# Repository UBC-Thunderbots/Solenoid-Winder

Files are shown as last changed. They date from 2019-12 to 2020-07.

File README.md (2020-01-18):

# Solenoid Winder

This is a project to produce a solenoid winding machine to wind the solenoids
for UBC ThunderBots. It uses a design inspired by a 3D printer z-axis to
guide the wire onto a rotating solenoid body.

We use a control board designed for a laser cutter or other small CNC machine
to drive the steppers. The particular one used is the
["Akozon 3D Printer Engraving Expansion Board Kit Controller CNC Shield V4"](https://www.amazon.ca/gp/product/B07DS2T64W/)
with the Arduino Nano clone that comes with it. It should be noted that this
board contains a bug: the microstepping jumpers are configured to pull down
the configuration pins on the drivers (which have internal pull-downs),
meaning that there is no way to set the MS1, MS2 or MS3 pins to high. Due to
this bug, the drivers are forced to full steps. We may hack the stepper
driver boards so they have a bodge wire to directly pull these pins up and
cut the pins going to the buggy mainboard.

The winder is controlled by serial commands. I suggest
[CompuPhase Termite](https://www.compuphase.com/software_termite.htm) on
Windows to control the winder.

### Setup

The solenoid winder board must be connected to a 12v source. We usually use
one of the ThunderBots lab power supplies, set to a current of 1.5A. This
*only* powers the stepper motors, meaning that you can use the serial command
line interface without the external power on.

Due to the habit of the rotational stepper motor to heat up uncomfortably
quickly when it is left on, it is advised to turn off the power supply while
not actively winding. It is a possible future project to replace this stepper
with one that doesn't do that.

Attach the core to the rotational hub with M3 socket head cap screws (keep
these in the hub while not in use!). Feed the wire through the arm on the
carriage, then through one of the four holes in the solenoid core to retain
the end. These are slightly tricky to get the wire through: curve it slightly
to help it along.

Set up the spool holder at least 30cm away from the winder while in use in
order to avoid any possible inconsistencies caused by winding of the source
spool. I usually use a big bar clamp to stick it to the table.

If the winder is doing something bad, you can stop it by pressing the reset
button on the blue microcontroller board, or by turning off the motor power
supply. Either of these actions will safely bring the winder to a halt.

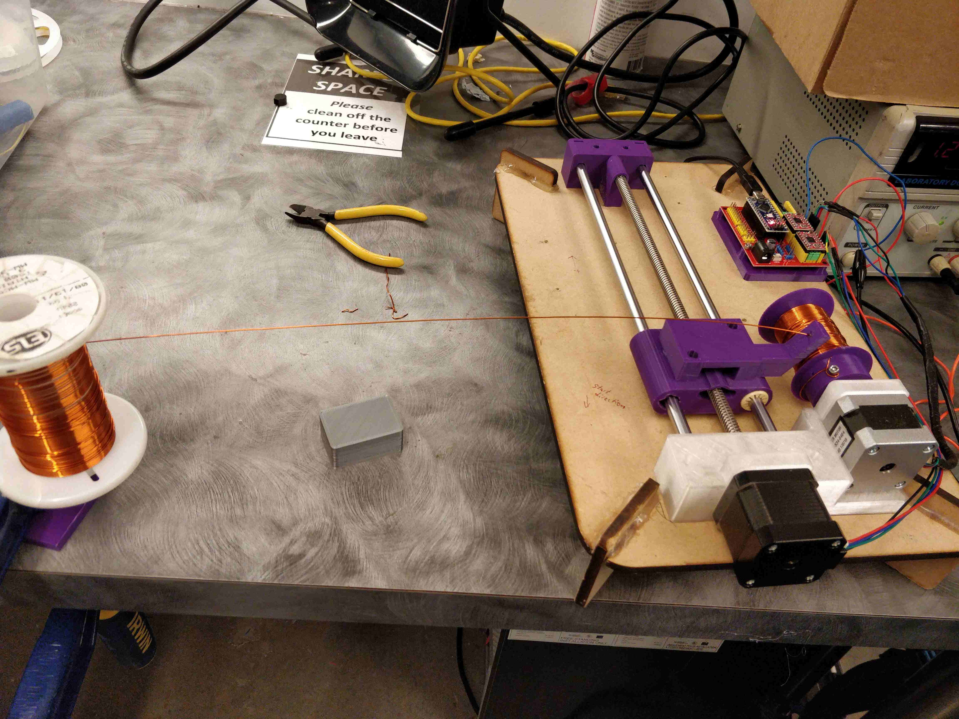
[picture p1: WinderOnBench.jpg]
photo of winder on the bench


### Operation

Set up your spool width with `spool_width {width in mm}`. Note that you
should set this about 5mm shorter than the actual spool width to avoid
overshooting the end of the spool.

Set the wire width: `wire_width {width in mm}`. This should have a
fudge-factor on it (oversize by ~5%) to ensure that the wire does not
inadvertently wind backwards: the current design of having an arm fairly
close to the spool means that if the winder does start winding in a backwards
direction, it can get back on track, but it is likely a better idea to simply
wind with a tiny bit of extra room.

Then, you can move the carriage either by slowly rotating the lead screw by
hand with the power off or by using `move_lateral {distance_in_mm}`. Note
that the positive direction is marked on the base of the winder and is
oriented away from the stepper on the lead screw.

Once you have the spool width and the wire width set up, you can start
winding by running `go {n_passes}`.

The winder will wind initially in the positive direction as marked on the
board (away from the rotational motor).

Note that each winding back and forth is
counted as two passes. See the diagram below:

```
║     ║        ║     ║
║     ║        ║_____║
╠═════╣ ---->  ╠═════╣
║    ↑║ 1 pass ║‾‾‾‾‾║
║    |║        ║↑    ║
    arm        arm
```

Also, the direction is reversed after every pass but is retained between runs
of the `go` command. This means that if you have already wound some turns and
want to wind some more, you can safely type `go 1` for example, and put on
another layer. If you want to start from the beginning, type `reset`.

Some tension is required on the wire in order to get it to go on straight.
This can be achieved by putting one's finger on the spool or with something
more advanced. Also, the winder itself is not really possible to clamp to the
table and wants to slide around.

## Development

This project is developed using [PlatformIO](https://platformio.org/).

To build from the command line: `platformio run`

To upload from the command line (note that you need to disconnect your
Termite window before uploading or it will fail to upload):
`platformio run -t upload`.

## Board documentation

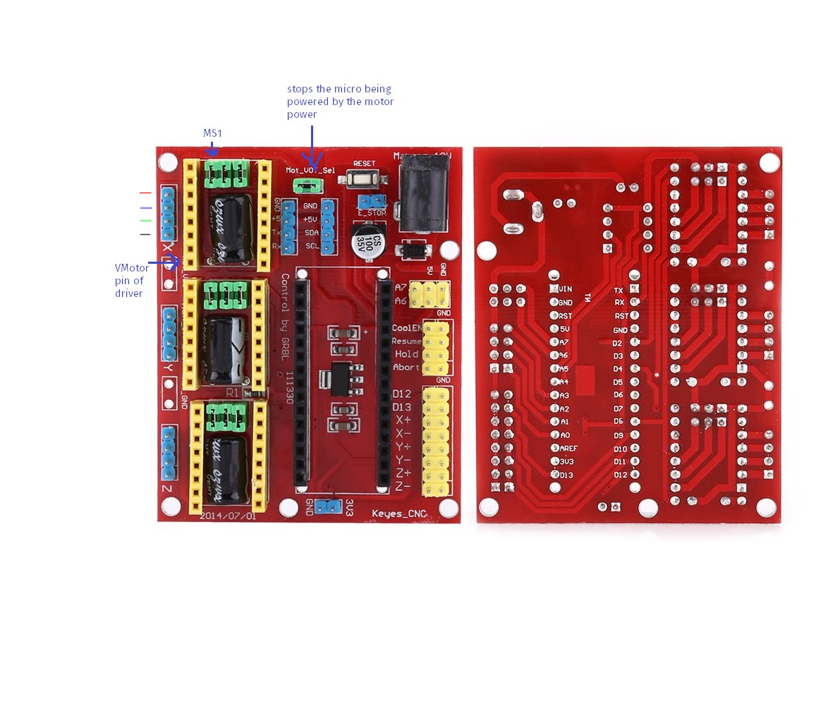
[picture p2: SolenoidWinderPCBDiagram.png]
board docs photo


## Future improvements

- Replace the rotational stepper motor with one that doesn't heat up quite as
  much
- Change the feet to something more flat and sturdy so it is possible to
  clamp the winder to the table
- Put proper connectors on the power input and stepper motors
- Tailstock?
- Hack the stepper driver boards by installing bodge wires and cutting the
  CFG pins on the headers so we get microstepping (currently it does full
  stepping because of a bug in the control board where the configuration pins
  should have a pull-up on the other side of the jumpers but actually have a
  pull-down)

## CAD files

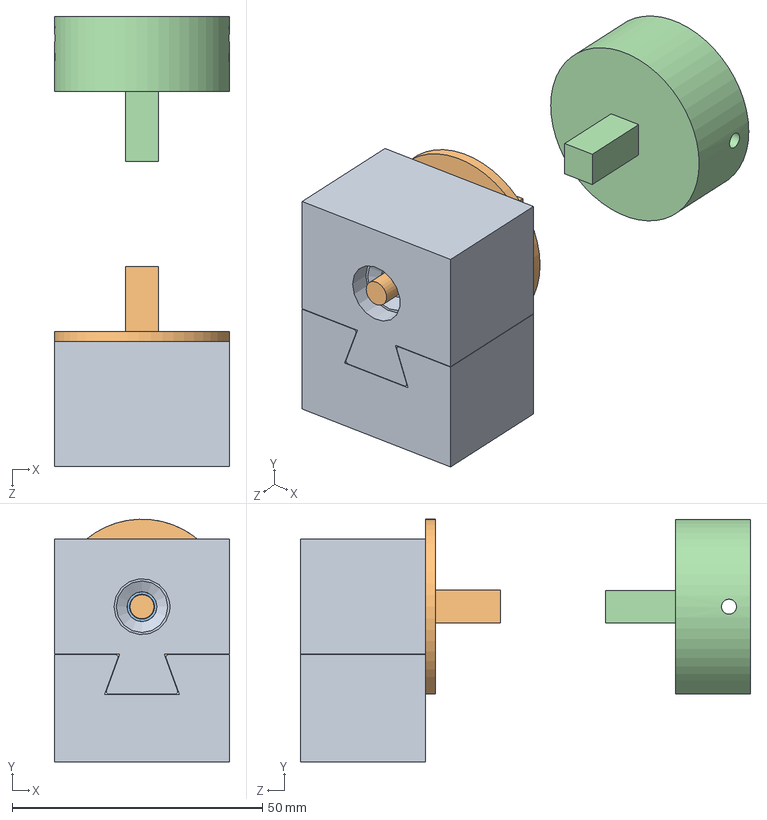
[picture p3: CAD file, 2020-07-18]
CAD/ThunderBots 2020 Headstock and Tailstock.SLDASM
35.0 x 48.5 x 90.0 mm
Tailstock Mount
Tailstock
bearing
SquareHub

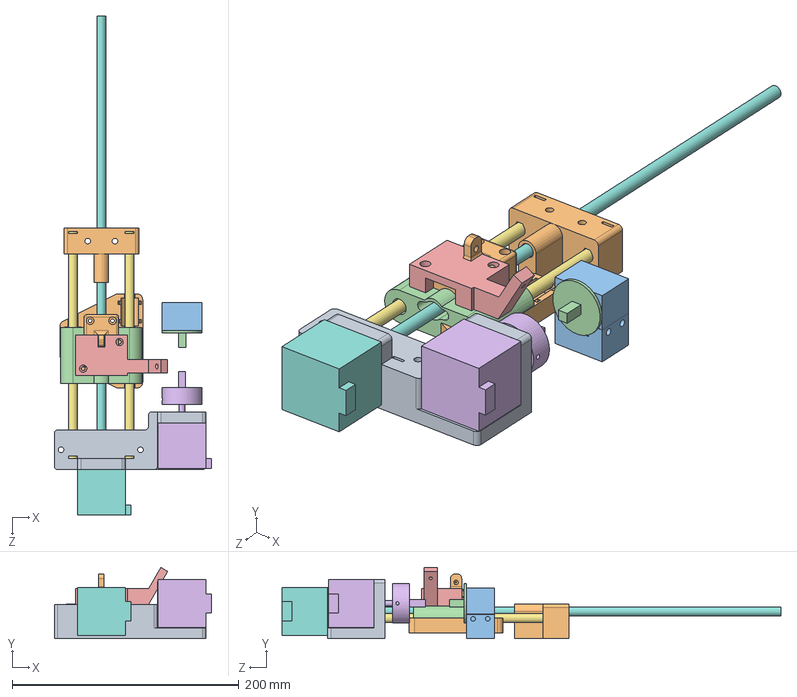
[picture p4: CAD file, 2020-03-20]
CAD/FullWinder.SLDASM
138.8 x 62.8 x 440.0 mm
SpinnyLeadScrewNut
New Main Part^Carriage
V2 Guide^Carriage
NormalStepper
Rod^FullWinder x 2
MotorEndBracket^FullWinder
Free End Cap^FullWinder
Tailstock Mount
Tailstock
bearing x 2
SquareHub

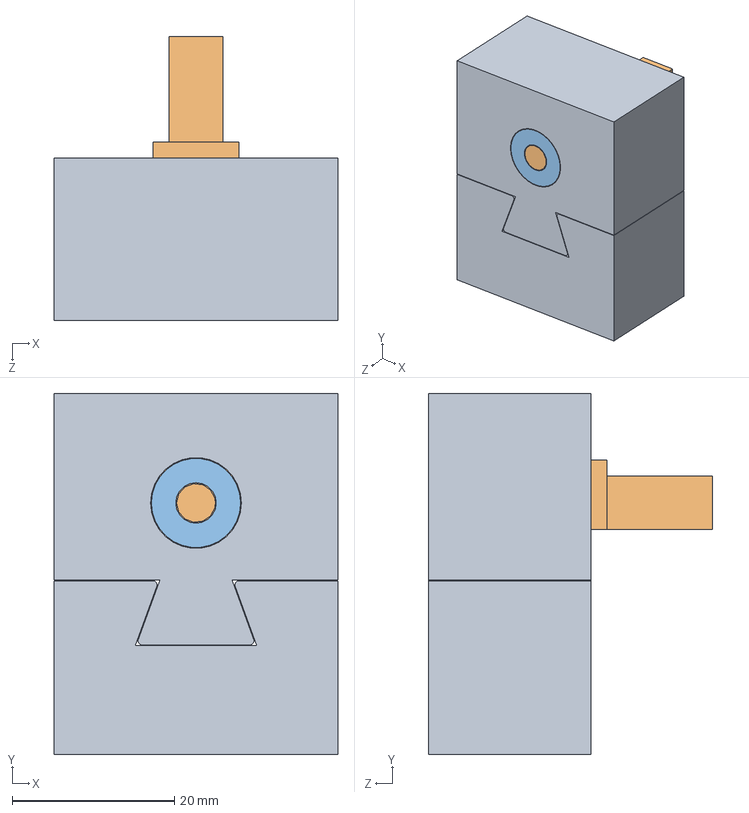
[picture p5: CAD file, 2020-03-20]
CAD/ThunderBots 2020/TailstockAssembly.SLDASM
35.0 x 44.5 x 35.0 mm
Tailstock Mount
Tailstock
bearing x 2

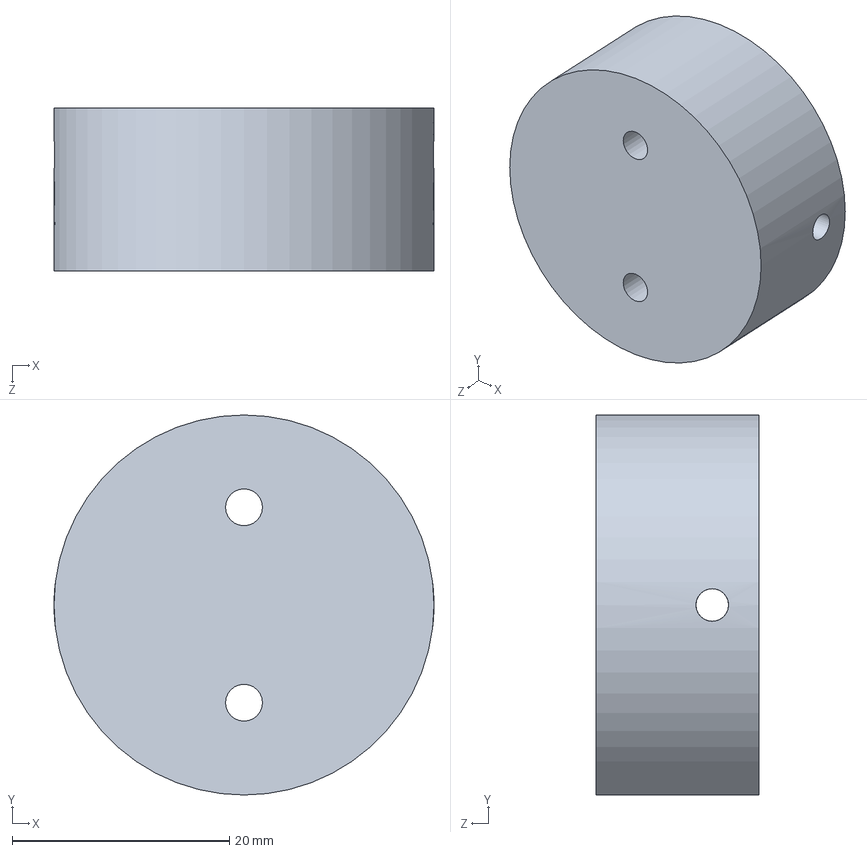
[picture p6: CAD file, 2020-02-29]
CAD/Hub^FullWinder.sldprt
35.0 x 35.0 x 15.0 mm

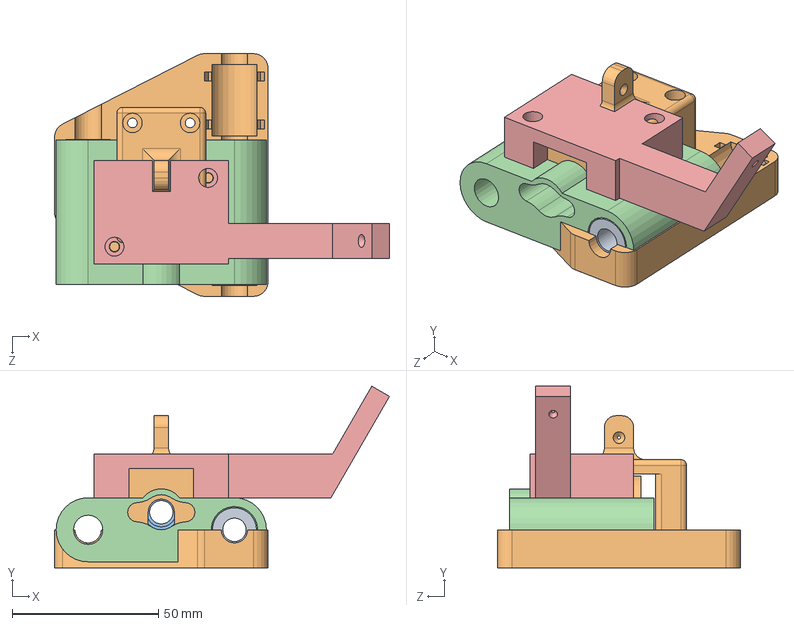
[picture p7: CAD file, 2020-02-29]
CAD/Carriage.SLDASM
114.5 x 62.1 x 83.0 mm
SpinnyLeadScrewNut
New Main Part^Carriage
V2 Guide^Carriage

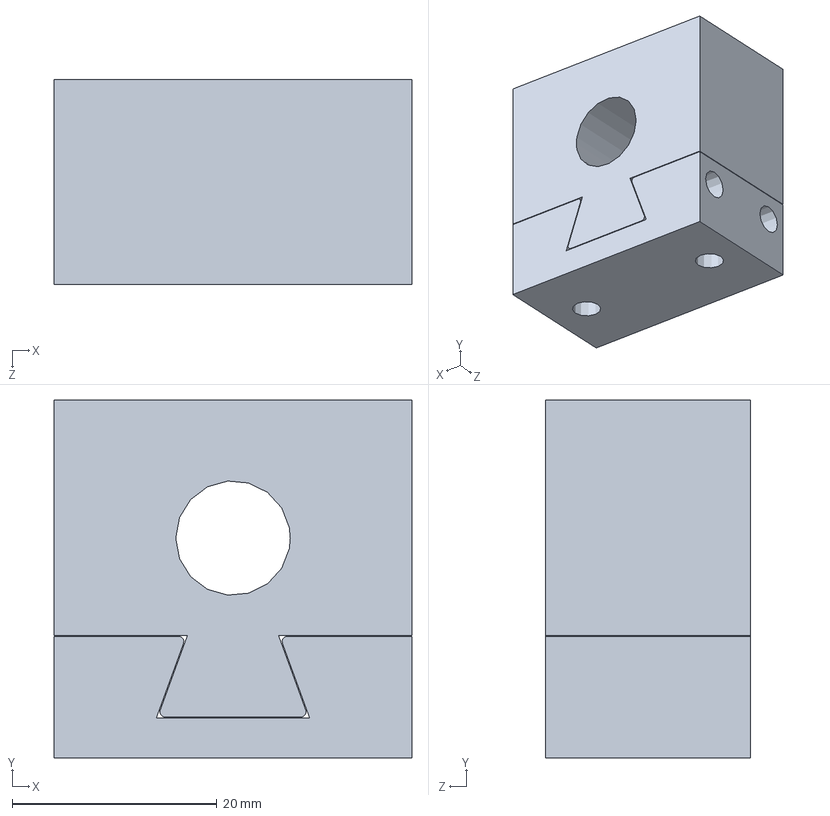
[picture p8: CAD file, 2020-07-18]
CAD/ThunderBots 2020/Tailstock Mount.SLDPRT
35.0 x 35.0 x 20.0 mm

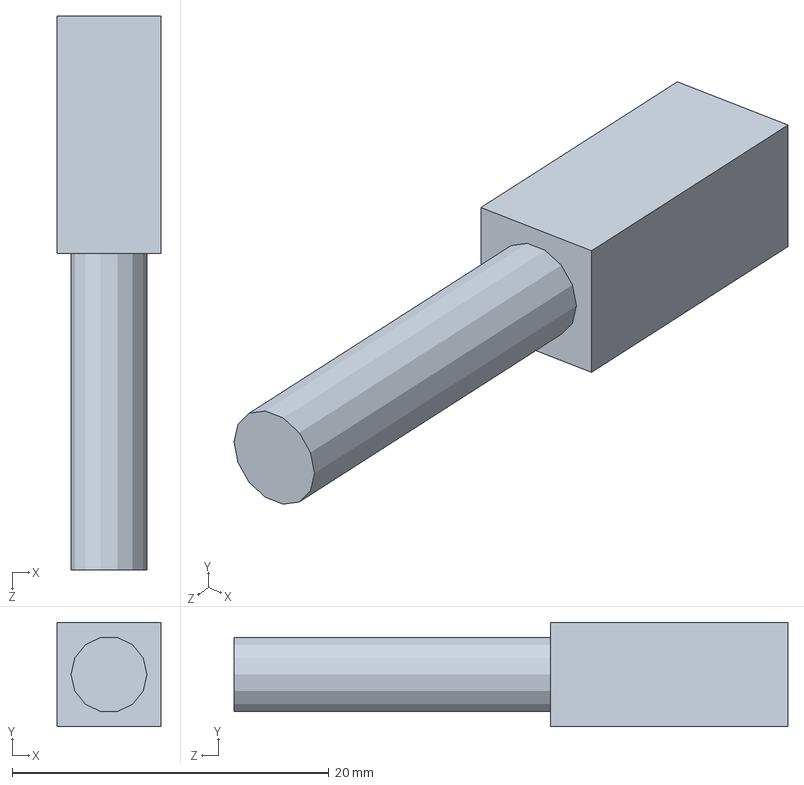
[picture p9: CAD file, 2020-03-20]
CAD/ThunderBots 2020/Tailstock.SLDPRT
6.60 x 6.60 x 35.0 mm

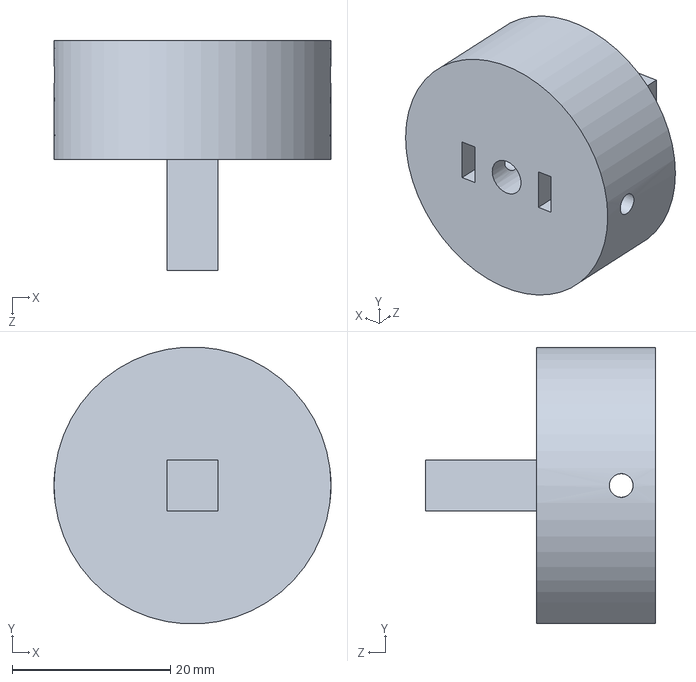
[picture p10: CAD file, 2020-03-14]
CAD/ThunderBots 2020/SquareHub.SLDPRT
35.0 x 34.9 x 29.0 mm

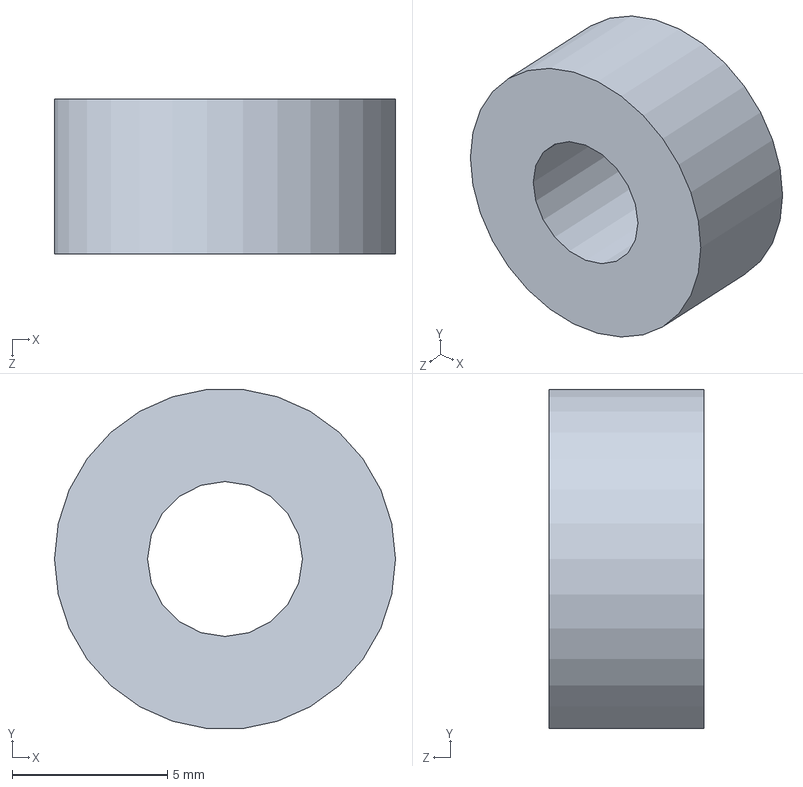
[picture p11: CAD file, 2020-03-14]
CAD/ThunderBots 2020/bearing.SLDPRT
11.0 x 10.9 x 5.00 mm

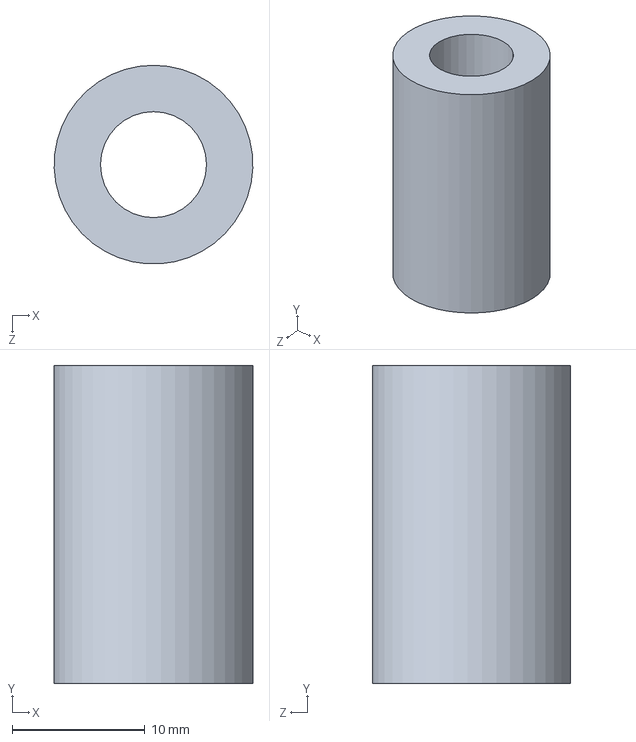
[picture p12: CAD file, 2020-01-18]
CAD/lm8uu.SLDPRT
15.0 x 24.0 x 15.0 mm

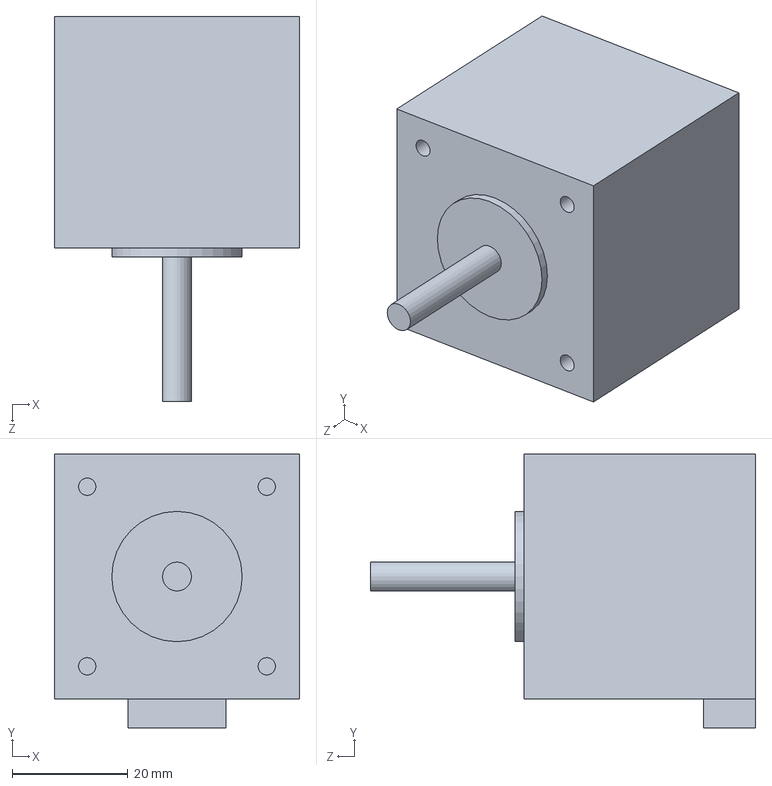
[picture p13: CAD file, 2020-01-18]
CAD/NormalStepper.SLDPRT
42.3 x 47.3 x 66.5 mm

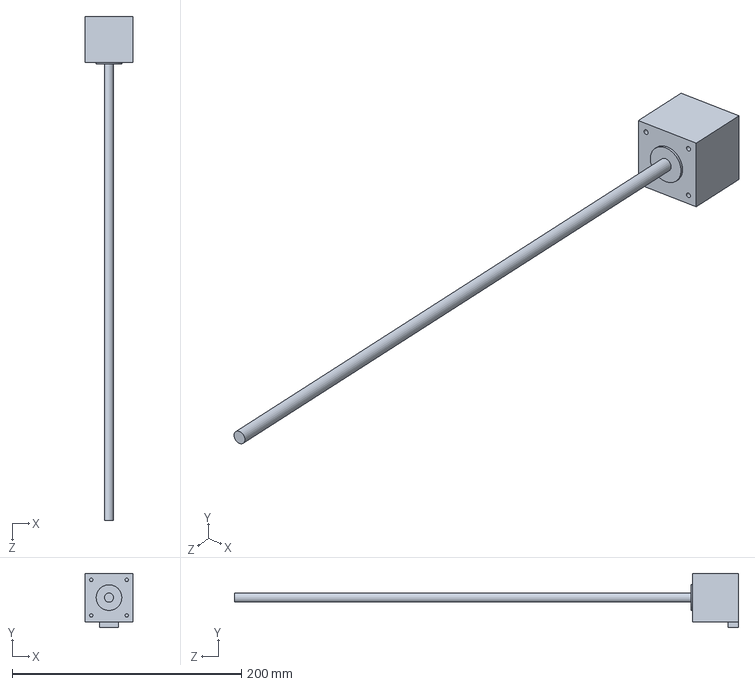
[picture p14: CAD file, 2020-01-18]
CAD/LeadScrewStepper.SLDPRT
42.3 x 47.3 x 440.0 mm

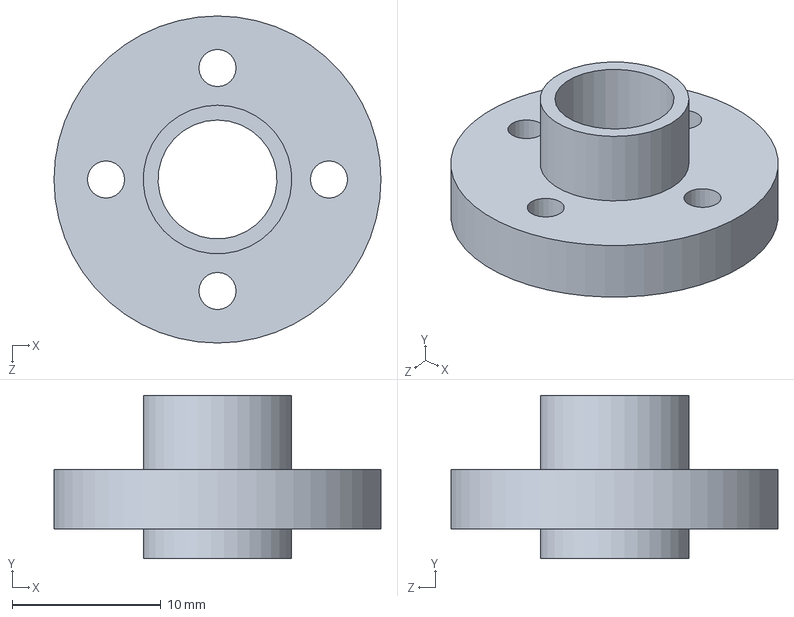
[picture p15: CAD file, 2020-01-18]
CAD/SpinnyLeadScrewNut.SLDPRT
22.0 x 11.0 x 22.0 mm

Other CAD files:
CAD/Test Hub and Solenoids.sldasm
CAD/Round Core.sldprt

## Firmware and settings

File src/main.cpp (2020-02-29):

#include "libraries.hpp"
#include "serialparser/serialparser.hpp"
#include "util.hpp"

// mm
float wire_width = 0.8118;
float spool_width = 25;

float running = false;
uint16_t n_passes = 0;
int8_t direction = 1;

namespace Pins {
int const M1STEP = 5;  // D5
int const M1DIR = 2;   // D2

int const M2STEP = 6;  // D6
int const M2DIR = 3;   // D3

int const ENABLE = 8;  // D8
}  // namespace Pins

long const MICROSTEPS = 1;

// 1.8-degree stepper
long const STEPS_PER_REV = MICROSTEPS * 200;

// for whatever reason it is going 4x as many steps as it should be going
float const MAGIC_NUMBER = 4.f;

// 1.8-degree stepper;
// 2mm pitch T8 thread
float const STEPS_PER_MM = STEPS_PER_REV / 2.f /* mm/rev */ / MAGIC_NUMBER;

auto lateral_stepper =
    AccelStepper{AccelStepper::DRIVER, Pins::M1STEP, Pins::M1DIR};
auto rotational_stepper =
    AccelStepper{AccelStepper::DRIVER, Pins::M2STEP, Pins::M2DIR};
auto both = MultiStepper{};

float revs_for_lateral_dist(float dist) { return (dist / wire_width); }

long steps_for_revs(float revs) { return revs * STEPS_PER_REV; }

long steps_for_lateral_mm(float dist) { return dist * STEPS_PER_MM; }

void print_help_messages() {
    Serial.print(
        F("Commands:\n"
          "wire_width {wire width in mm}\n"
          "spool_width {spool width in mm}\n"
          "speed {arbitrary unit}\n"
          "go {n_passes}: START: do this many passes back and forth\n"
          "move_lateral {mm}\n"
          "move_rotational {turns}\n"
          "invert_direction -- reverse winding direction from current state\n"
          "reset -- set default parameters, initial direction\n"));
}

void move_both(long rotational, long lateral) {
    long moves[] = {rotational, lateral};
    both.moveTo(moves);
}

void move_dist_synchronized(float dist) {
    move_both(steps_for_revs(revs_for_lateral_dist(abs(dist))),
              steps_for_lateral_mm(dist));
}

void clear_positions() {
    // Clear positions so we are moving relative to physical position
    lateral_stepper.setCurrentPosition(0);
    rotational_stepper.setCurrentPosition(0);
}

void reset() {
    lateral_stepper.setAcceleration(1000);
    rotational_stepper.setAcceleration(1000);
    lateral_stepper.setMaxSpeed(100);
    lateral_stepper.setSpeed(100);
    rotational_stepper.setMaxSpeed(100);
    rotational_stepper.setSpeed(100);
    direction = 1;
    running = false;
}

void blink(int pin, int time_ms) {
    digitalWrite(pin, HIGH);
    delay(time_ms);
    digitalWrite(pin, LOW);
}

void print_status() {
    Serial.print("Wire width: ");
    Serial.print(wire_width);
    Serial.print(", Spool width: ");
    Serial.print(spool_width);
    Serial.print(", Winding towards ");
    Serial.print(direction == 1 ? '+' : '-');
    Serial.print("X\n");
}

void handle_serial_command() {
    auto res = serialparser::parse(&Serial);
    switch (res.cmd) {
        case serialparser::Command::Go:
            Serial.println(F("Going!!"));
            n_passes = floor(res.args[0]);
            running = true;

            // sinful; basically we want it to start in the same direction as it
            // did the last round in, so we negate the direction = -direction in
            // the running loop here
            direction = -direction;

            lateral_stepper.setAcceleration(1000);
            rotational_stepper.setAcceleration(1000);
            // lateral_stepper.move(res.args[0] * 8000);
            // lateral_stepper.runToPosition();
            break;

        case serialparser::Command::Speed:
            Serial.print(F("Speed is now: "));
            Serial.println(res.args[0]);
            lateral_stepper.setMaxSpeed(res.args[0]);
            lateral_stepper.setSpeed(res.args[0]);
            rotational_stepper.setMaxSpeed(res.args[0]);
            rotational_stepper.setSpeed(res.args[0]);
            break;

        case serialparser::Command::SpoolWidth:
            Serial.print(F("SpoolWidth is now: "));
            Serial.println(res.args[0]);
            spool_width = res.args[0];
            break;

        case serialparser::Command::WireWidth:
            Serial.print(F("WireWidth is now: "));
            Serial.println(res.args[0]);
            wire_width = res.args[0];
            break;

        case serialparser::Command::MoveLateral:
            Serial.print(F("Moving lateral [mm]: "));
            Serial.println(res.args[0]);
            Serial.println(steps_for_lateral_mm(res.args[0]));
            lateral_stepper.move(steps_for_lateral_mm(res.args[0]));
            while (lateral_stepper.run())
                ;
            break;

        case serialparser::Command::MoveRotational:
            Serial.print(F("Moving rotational [turns]: "));
            Serial.println(res.args[0]);
            Serial.println(steps_for_revs(res.args[0]));
            rotational_stepper.move(steps_for_revs(res.args[0]));
            while (rotational_stepper.run())
                ;
            break;

        case serialparser::Command::InvertDirection:
            Serial.print(F("Inverting wind direction, now "));
            direction = -direction;
            Serial.println(direction);
            break;

        case serialparser::Command::Reset:
            reset();
            break;

        case serialparser::Command::None:
        default:
            Serial.println(F("Unknown command"));
            break;
    }
    if (res.cmd != serialparser::Command::Go) {
        // don't print status report when running a Go because it will report a
        // confusing and incorrect winding direction as of the time the winding
        // completes (it will have been inverted by the time you run the
        // command)
        print_status();
    }
}

void setup() {
    Serial.begin(9600);
    pinMode(Pins::ENABLE, OUTPUT);
    digitalWrite(Pins::ENABLE, 0);  // active low
    print_help_messages();
    both.addStepper(rotational_stepper);
    both.addStepper(lateral_stepper);
    reset();
    print_status();

    while (true) {
        if (running) {
            both.run();
            if (lateral_stepper.currentPosition() ==
                    lateral_stepper.targetPosition() &&
                rotational_stepper.currentPosition() ==
                    rotational_stepper.targetPosition()) {
                clear_positions();
                direction = -direction;

                // done all the winding
                if (n_passes == 0) {
                    Serial.println(F("Done!"));
                    running = false;
                    continue;  // stop running this routine
                }
                --n_passes;
                blink(LED_BUILTIN, 250);
                delay(100);
                blink(LED_BUILTIN, 250);
                Serial.print(F("pass done! "));
                Serial.print(n_passes);
                Serial.println(F(" remaining"));
                move_dist_synchronized(direction * spool_width);
            }
        }
        if (Serial.available() > 0) {
            handle_serial_command();
        }
    }
}

void loop() {}

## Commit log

2019-12-14 `reset` command now stops active winding operation
    [main.cpp]
2019-12-14 Add docs on how to actually wind solenoids
2020-01-18 Change the default wind direction to wind away from the rotation stepper
2020-01-18 Add CAD files, a license
    [Carriage.SLDASM, FullWinder.SLDASM, Hub^FullWinder.sldprt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]
2020-02-29 Maybe solidworks will open it now
    [Carriage.SLDASM, FullWinder.SLDASM, Hub^FullWinder.sldprt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]
2020-03-14 add configuration for the tbots 2020 solenoid
    [FullWinder.SLDASM, Round Core.sldprt, SquareHub.SLDPRT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]
2020-03-20 Add a chonky flange on the tailstock center
    Though this makes it moderately more annoying to print, it allows us to
    wind chipper solenoids directly on the device without using end caps.
    [FullWinder.SLDASM, Tailstock Mount.SLDPRT, Tailstock.SLDPRT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]
2020-07-18 Add bearing seats for tailstock bearings
    [Tailstock Mount.SLDPRT, ThunderBots 2020 Headstock and Tailstock.SLDASM]
